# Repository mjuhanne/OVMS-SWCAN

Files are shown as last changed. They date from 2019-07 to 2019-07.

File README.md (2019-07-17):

# OVMS SWCAN add-on board

This add-on board for [OVMS (Open Vehicle Monitoring System)](https://www.openvehicles.com/) adds Single-Wire CAN (GMLAN) functionality to OVMS 3.0 module.

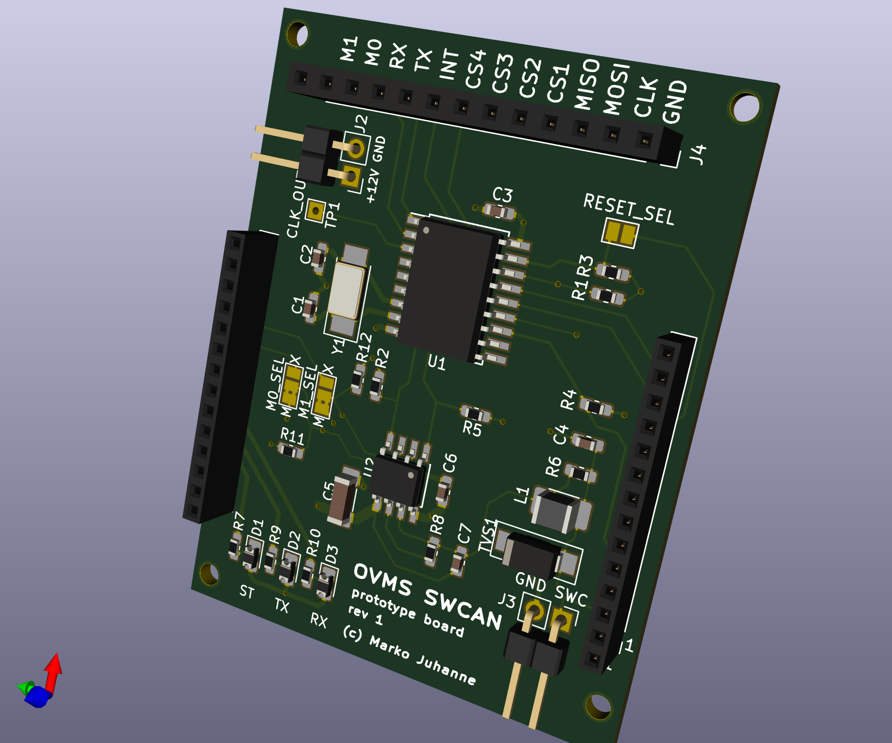
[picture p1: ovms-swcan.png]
OVMS SWCAN prototype board rev 1


This board uses the same MCP2515 CAN controller as OVMS module, but instead of SN65 transceiver it employs TH8056 which fully supports SWCAN capabilities. While SN65 (and other CAN transceivers) can be used to receive/transmit CAN messages on SWCAN bus, they unfortunately are unable to wake the car with the so called **High-Voltage Wake Up** (which pulls CAN bus line up to 12V). Thus OVMS hasn't been so useful so far with those cars with most of the interesting communication done on SWCAN bus (such as GM/Chevrolet brands). 

This add-on board adds the full support for SWCAN communication and allows such remote functionality as locking/unlocking the car, cabinet/engine preheating, polling environmental variables (such as cabin temperature) even when the car is asleep. The SWCAN circuitry is heavily inspired by same implementation found on [Macchina M2](https://www.macchina.cc/) interface board. However this board is designed to connect directly to the OVMS extension header and to fit inside the existing plastic case on top of the optional GSM/GPS module.

In addition to SWCAN bus functionality, there are also 3 LEDS, various debugging test points and a 13 pin header to facilitate easier connection to logic analyzer. 

As for software, see [my GitHub repository](https://github.com/mjuhanne/Open-Vehicle-Monitoring-System-3) which has patches for OVMS to enable support for this add-on board. It contains also additional functionality for Chevrolet Volt / Opel Ampera.

### Connection to SWCAN bus

To physically connect the SWCAN bus lines to the board, there are several ways. 
  1. Use the 2-pin SWCAN header on the board. (SWCAN_LO is GND by standard) 
  2. Connect the SWCAN_HI to pin 19 (GEP_1) on DB25 extension port.
  3. Create OBD cable that connects the SWCAN bus to the unused pin 1 on OVMS DB9 port. Then solder a jumper wire from that pin 1 to the GEP_1 on OVMS extension header. 
  4. Substitute the CAN2 with SWCAN: Create OBD cable so that GND is attached to CAN2_LO and SWCAN_HI to CAN2_HI. Then connect pin 16 (CAN2_HI) to pin 19 on DB25 (or use the dongle mentioned below). This actually then replaces the third CAN bus (CAN2) and the second internal MCP2515, which is put to sleep with modified OVMS code. This approach doesn't require internal modification of the OVMS module.

The cable I use with my Opel Ampera / Chevrolet Volt uses the approach #4:

| OBD-pin | DB9-pin | Comment |
| --- | --- | --- |
| 1 | 8 | SWCAN_HI --> CAN2_HI  | 
| 4 | 6 | CHASSIS & SIGNAL GND --> CAN2_LO | 
| 4 | 3 | CHASSIS & SIGNAL GND | 
| 6 | 7 | CAN0_HI (Primary High-Speed CAN) | 
| 14 | 2 | CAN0_LO (Primary High-Speed CAN) | 
| 12 | 5 | CAN1_HI (Secondary High-Speed CAN) | 
| 13 | 4 | CAN1_LO (Secondary High-Speed CAN) | 
| 16 | 9 | +12V | 

### Technical details and debugging

The TH8056 transceiver modes (normal, sleep, high-voltage, high speed) are controlled either indirectly with MCP2515 controller (default setting, changeable with M0_SEL and M1_SEL jumpers) or directly with MAX7317 EGPIO pins. This latter approach was a backup option in case MCP2515 turned out to be finicky, but it seems this is not the case. So, the available MAX7317 pins can be used for other uses, for example for test buttons connected to GEP_4 and GEP_3 (connect jumpers BTN1_SEL and BTN2_SEL in this case). 

In case you want to debug the SPI bus with all the CS lines from various peripherals connected at the same time, it's easier to solder jumper wires from the ESP32 to GEP #2-#4, which are routed on the the add-on board to the 13 pin header. Then hooking/unhooking a logic analyzer wires becomes a breeze. Note that the CS line of MCP2515 of this add-on board is wired already to the header, so no need for soldering if you need to debug only the SPI traffic on the SWCAN controller.

To allow doing a hardware reset on MCP2515 via MAX7317, connect RESET_SEL jumper and then drive EGPIO_3 low.

### Optional debugging dongle
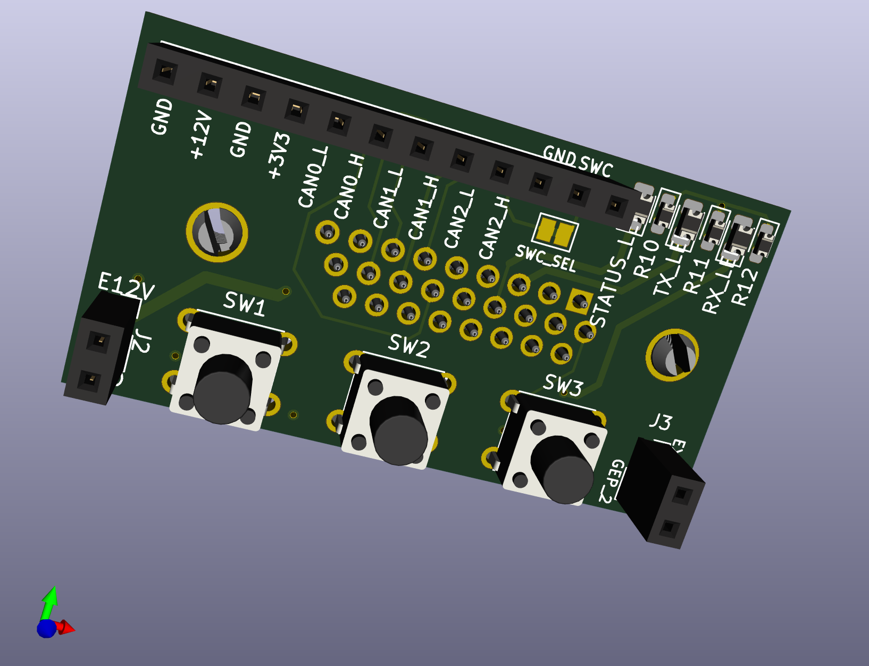
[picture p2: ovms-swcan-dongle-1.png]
Debugging dongle


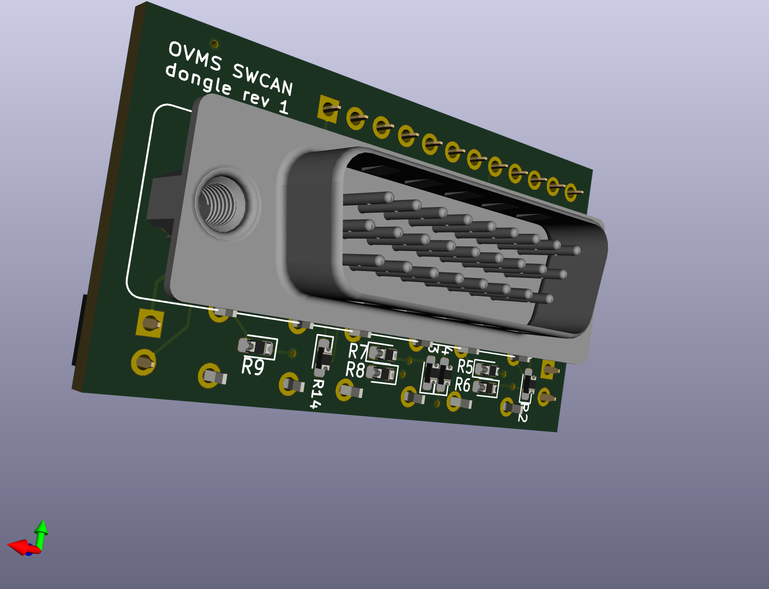
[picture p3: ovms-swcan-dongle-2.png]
Debugging dongle


Included in this repository is also an optional debugging dongle that contains following functionality:
   - Placeholders for 3 hardware buttons, of which the first two (BTN1 and BTN2) can be tailored in varied pull-up/pull-down/RC debouncing configurations. They can be polled with MAX7317. BTN3 is a pull-down button connected to EXP_1/SWCAN_INT that can induce interrupt if needed (for example to awake the OVMS from sleep state for testing purposes)
   - STATUS/TX/RX leds (wired in parallel with internal LEDS) so that they can be seen also with the case on.
   - 12V / EXT_12V and 3.3V pins
   - CAN0, CAN1, CAN2 and SWCAN bus pins
   - By default the CAN2_HI is connected to SWCAN_HI to avoid internal jumper wires. This connection can be severed by disconnecting the SWC_SEL jumper with a sharpie.

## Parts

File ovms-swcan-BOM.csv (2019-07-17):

Id | Designator | Package | Quantity | Designation | Supplier and ref | Mouser ref | Comment
1 | JP6 | SolderJumper-2_P1.3mm_Open_Pad1.0x1.5mm | 1 | BTN2_SEL
2 | JP5 | SolderJumper-2_P1.3mm_Open_Pad1.0x1.5mm | 1 | BTN1_SEL
3 | C5 | C_1806_4516Metric_Pad1.57x1.80mm_HandSolder | 1 | 10uF
4 | U2 | SOIC-8_3.9x4.9mm_P1.27mm-HS | 1 | TH8056-KDC-A8 | TH8056KDC-AAA-008-RE | 482-8056KDCAAA008RE
5 | R10,R9,R7 | R_0603_1608Metric_Pad1.05x0.95mm_HandSolder | 3 | R
6 | D3 | D_0805_2012Metric_Pad1.15x1.40mm_HandSolder | 1 | RX_LED | LO L296-P1S1-24-Z | 720-LOL296P1S124Z | Orange LED
7 | D2 | D_0805_2012Metric_Pad1.15x1.40mm_HandSolder | 1 | TX_LED | VLMB1300-GS08 | 78-VLMB1300-GS08 | Blue LED
8 | D1 | D_0805_2012Metric_Pad1.15x1.40mm_HandSolder | 1 | STATUS_LED | LS L296-N1Q2-1-Z | 720-LSL296-N1Q2-1-Z | Red LED
9 | Y1 | NX5032GA-SMD_Crystal_2Pin_5.0x3.2mm_HandSoldering | 1 | Crystal | NX5032GA-16.000M-STD-CSU-2 | 344-NX5032GA16MCSU2
10 | U1 | SOIC-18W_7.5x11.6mm_P1.27mm_HS | 1 | MCP2515-E/SO | MCP2515-E/SO | 579-MCP2515-E/SO
11 | TVS1 | DO-214AC_Handsoldering | 1 | 22V | SMAJ22CA | 652-SMAJ22CA
12 | TP1 | TestPoint_THTPad_1.5x1.5mm_Drill0.7mm | 1 | TestPoint
13 | R12,R11,R4,R3,R2,R1 | R_0603_1608Metric_Pad1.05x0.95mm_HandSolder | 6 | 10K
14 | R8 | R_0603_1608Metric_Pad1.05x0.95mm_HandSolder | 1 | 6.49K
15 | R6 | R_0603_1608Metric_Pad1.05x0.95mm_HandSolder | 1 | 1K
16 | R5 | R_0603_1608Metric_Pad1.05x0.95mm_HandSolder | 1 | 10K?
17 | L1 | L_Custom_2.50x2.90mm_HandSolder | 1 | 47 uH | CM322522-470JL | 652-CM322522-470JL
18 | JP3 | SolderJumper-3_P1.3mm_Bridged2Bar12_Pad1.0x1.5mm_NumberLabels | 1 | M1_SEL
19 | JP2 | SolderJumper-3_P1.3mm_Bridged2Bar12_Pad1.0x1.5mm_NumberLabels | 1 | M0_SEL
20 | JP1 | SolderJumper-2_P1.3mm_Open_Pad1.0x1.5mm | 1 | RESET_SEL
21 | J4 | PinSocket_1x13_P2.54mm_Vertical | 1 | Conn_01x13_Male
22 | J3 | PinHeader_1x02_P2.54mm_Vertical | 1 | CONN_SWCAN
23 | J2 | PinHeader_1x02_P2.54mm_Vertical | 1 | CONN_PWR
24 | J1 | OVMS_V3.1_EXTENSION | 2 | OVMS-V3.1-EXPANSION | M22-2511405 | 855-M22-2511405 | 14-pin header, 2mm pitch
25 | C7 | C_0603_1608Metric_Pad1.05x0.95mm_HandSolder | 1 | 100pF
26 | C6,C3 | C_0603_1608Metric_Pad1.05x0.95mm_HandSolder | 2 | 100n
27 | C4 | C_0603_1608Metric_Pad1.05x0.95mm_HandSolder | 1 | 220pF
28 | C2,C1 | C_0603_1608Metric_Pad1.05x0.95mm_HandSolder | 2 | 9pF

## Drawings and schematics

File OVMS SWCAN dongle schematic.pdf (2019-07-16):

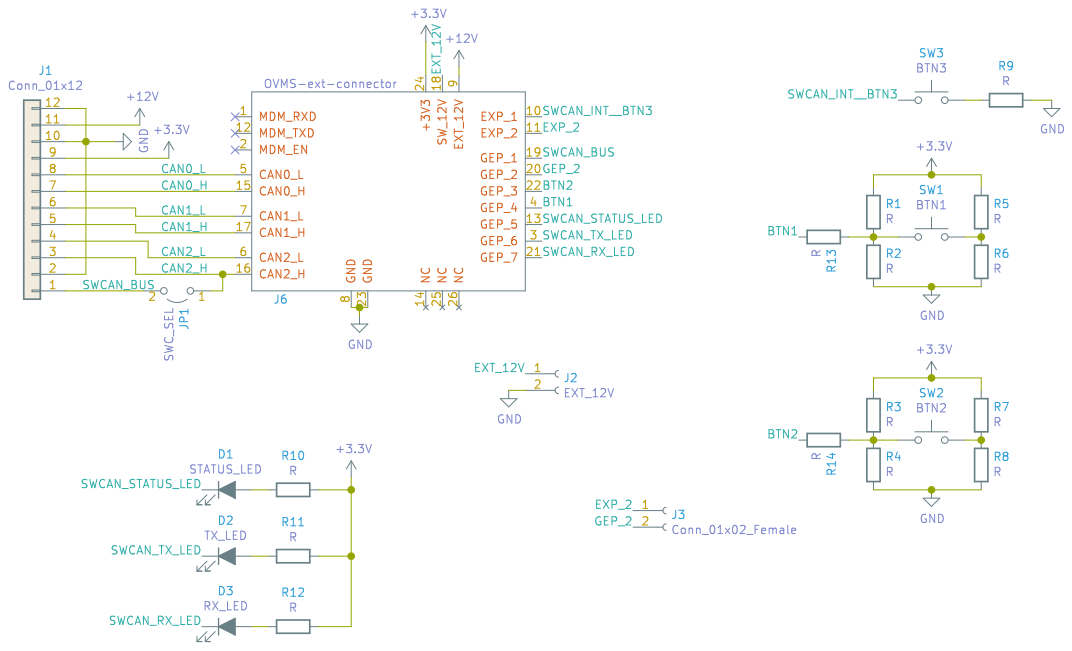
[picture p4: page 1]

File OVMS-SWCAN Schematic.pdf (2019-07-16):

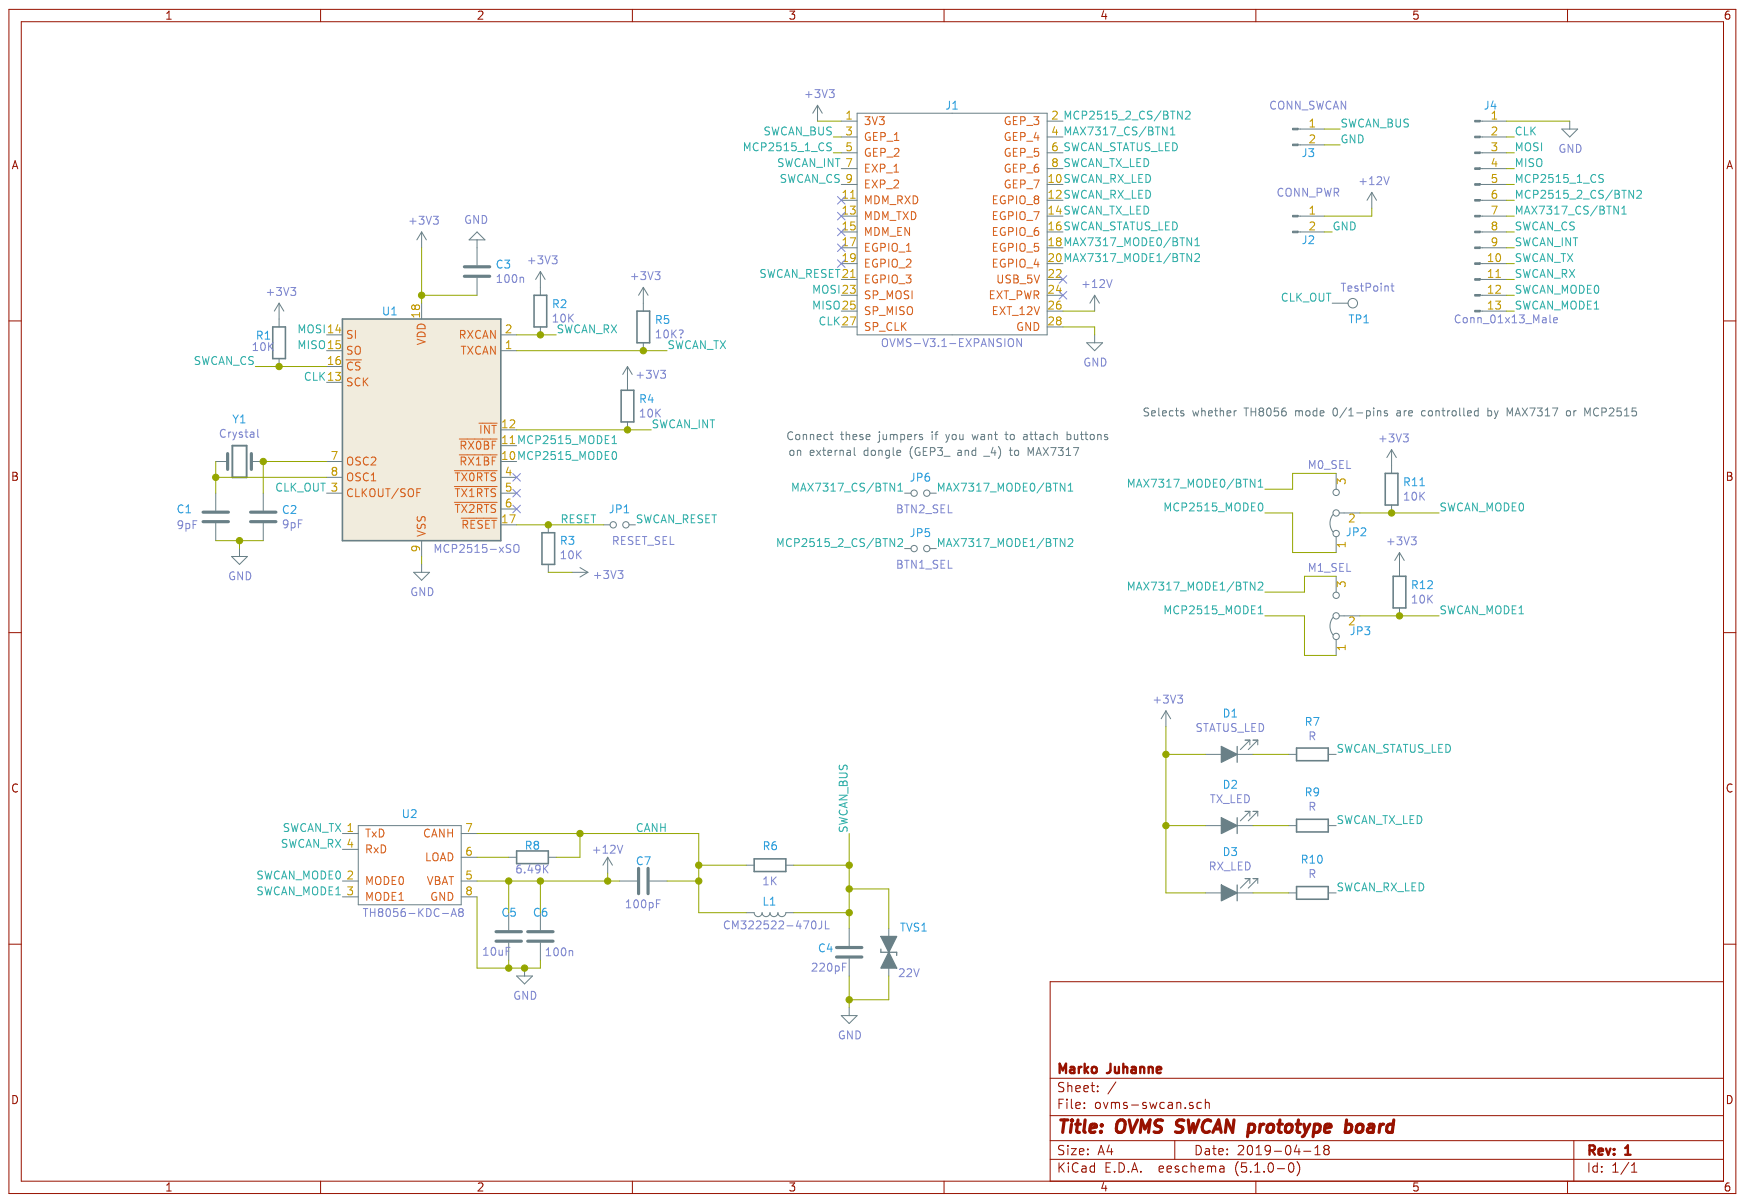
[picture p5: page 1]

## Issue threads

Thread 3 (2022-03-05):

4 Layer board?

kallisti5, 2022-03-05:
I tried to manufacture this, but it looks like a 4 layer board?
The complexity seems low, so really unsure why it's a 4 layer board. Shouldn't it be a two layer board?

Without the original kicad project files i'm unable to review + fix.  Are these around still?

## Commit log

2019-07-16 First commit.
    [ovms-swcan-dongle-NPTH.drl, ovms-swcan-dongle-PTH.drl, ovms-swcan-dongle.GBL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]
2019-07-16 Moved the panel gerbers to gerber subdirectory
    [panel.GBL, panel.GBO, panel.GBS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]
2019-07-16 Updated the gerbers
2019-07-17 Add board images
2019-07-17 Add bill of materials
    [ovms-swcan-BOM.csv]
